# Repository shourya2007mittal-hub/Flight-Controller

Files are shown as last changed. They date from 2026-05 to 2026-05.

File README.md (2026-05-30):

# Flight Controller

I am making a STM32F405RGT6 based flight controller for my drone.and has IMU and barometer and has a USB-B Type. It is designed for 4 motor drone. It has 4 layer PCB
<br>

<br>

## Features

Microcontroller: STM32F405RGT6<br>
IMU Sensor: MPU-6050 / ICM-2098<br>
Barometer: BMP280<br>

- ## Bill of Materials (BOM)
| Serial Num | Description | Total (USD) | 
|----:|---|---|
| 1  | PCB and Assembly  |167.50 |
| 2 | Shipping - Discount JLCPCB  |14.55 |

### 💰 Cost Summary

- **Estimated Total Cost ( PCB ASSEMBLY + Shipping):** **$182.05 USD**
 ## Schematic & PCB<br>
 



<br>

# 3d Render<br>



  <br>

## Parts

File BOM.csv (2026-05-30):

Item | Price | Source
PCB and Assembly | 167.5 | JLCPCB
Shipping - Discount JLCPCB | 14.55 | JLCPCB
Total | 182.05 | JLCPCB

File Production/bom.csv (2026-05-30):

Designator | Footprint | Quantity | Value | LCSC Part #
C1, C17, C28, C29, C9 | 603 | 5 | 10u | C96446
C10, C2, C21, C22, C23, C25, C26, C27, C3, C30, C31, C4, C5, C6, C7, C8 | 402 | 16 | 100n | C1525
C11, C12 | 603 | 2 | 10p | C1634
C13, C14, C15, C16 | 603 | 4 | 2u2 | C23630
C18 | 805 | 1 | 100n | C49678
C19, C20 | 805 | 2 | 22u | C45783
C24 | 603 | 1 | 2n2 | C1604
D1, D3 | 603 | 2 | LED | C2286
D2 | D_SOD-123 | 1 | b5819w | C8598
F1 | 603 | 1 | 500 mA | C20798
FB1, FB2 | 805 | 2 | 100R | C1015
L1 | L_Sunlord_SWPA4030S | 1 | 3.9uH | C96899
Q1 | SOT-23 | 1 | AO3401A | C15127
R1 | 603 | 1 | 10k | C25804
R2, R3, R5, R6 | 603 | 4 | 2k2 | C4190
R4, R7 | 603 | 2 | 1k | C21190
S1, S2 | SW_TS-1187A-B-A-B | 2 | TS-1187A-B-A-B | C318884
U1 | LQFP-64_10x10mm_P0.5mm | 1 | STM32F405RGTx | C15742
U2 | TSOT-23-6 | 1 | AP63203WU | C780769
U3 | SOT-23-6 | 1 | USBLC6-2SC6 | C7519
U4 | InvenSense_QFN-24_4x4mm_P0.5mm | 1 | MPU-6050 | C24112
U5 | InvenSense_QFN-24_3x3mm_P0.4mm | 1 | ICM-20948 | C726001
U6 | SOT-23-5 | 1 | LD39015M18R | C361025
U7 | TSSOP-14_4.4x5mm_P0.65mm | 1 | NTS0104PW | C2802637
U8 | Bosch_LGA-8_2x2.5mm_P0.65mm_ClockwisePinNumbering | 1 | BMP280 | C83291
Y1 | Crystal_SMD_3225-4Pin_3.2x2.5mm | 1 | 16Mhz | C13738

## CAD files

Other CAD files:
CAD/Controller.f3d

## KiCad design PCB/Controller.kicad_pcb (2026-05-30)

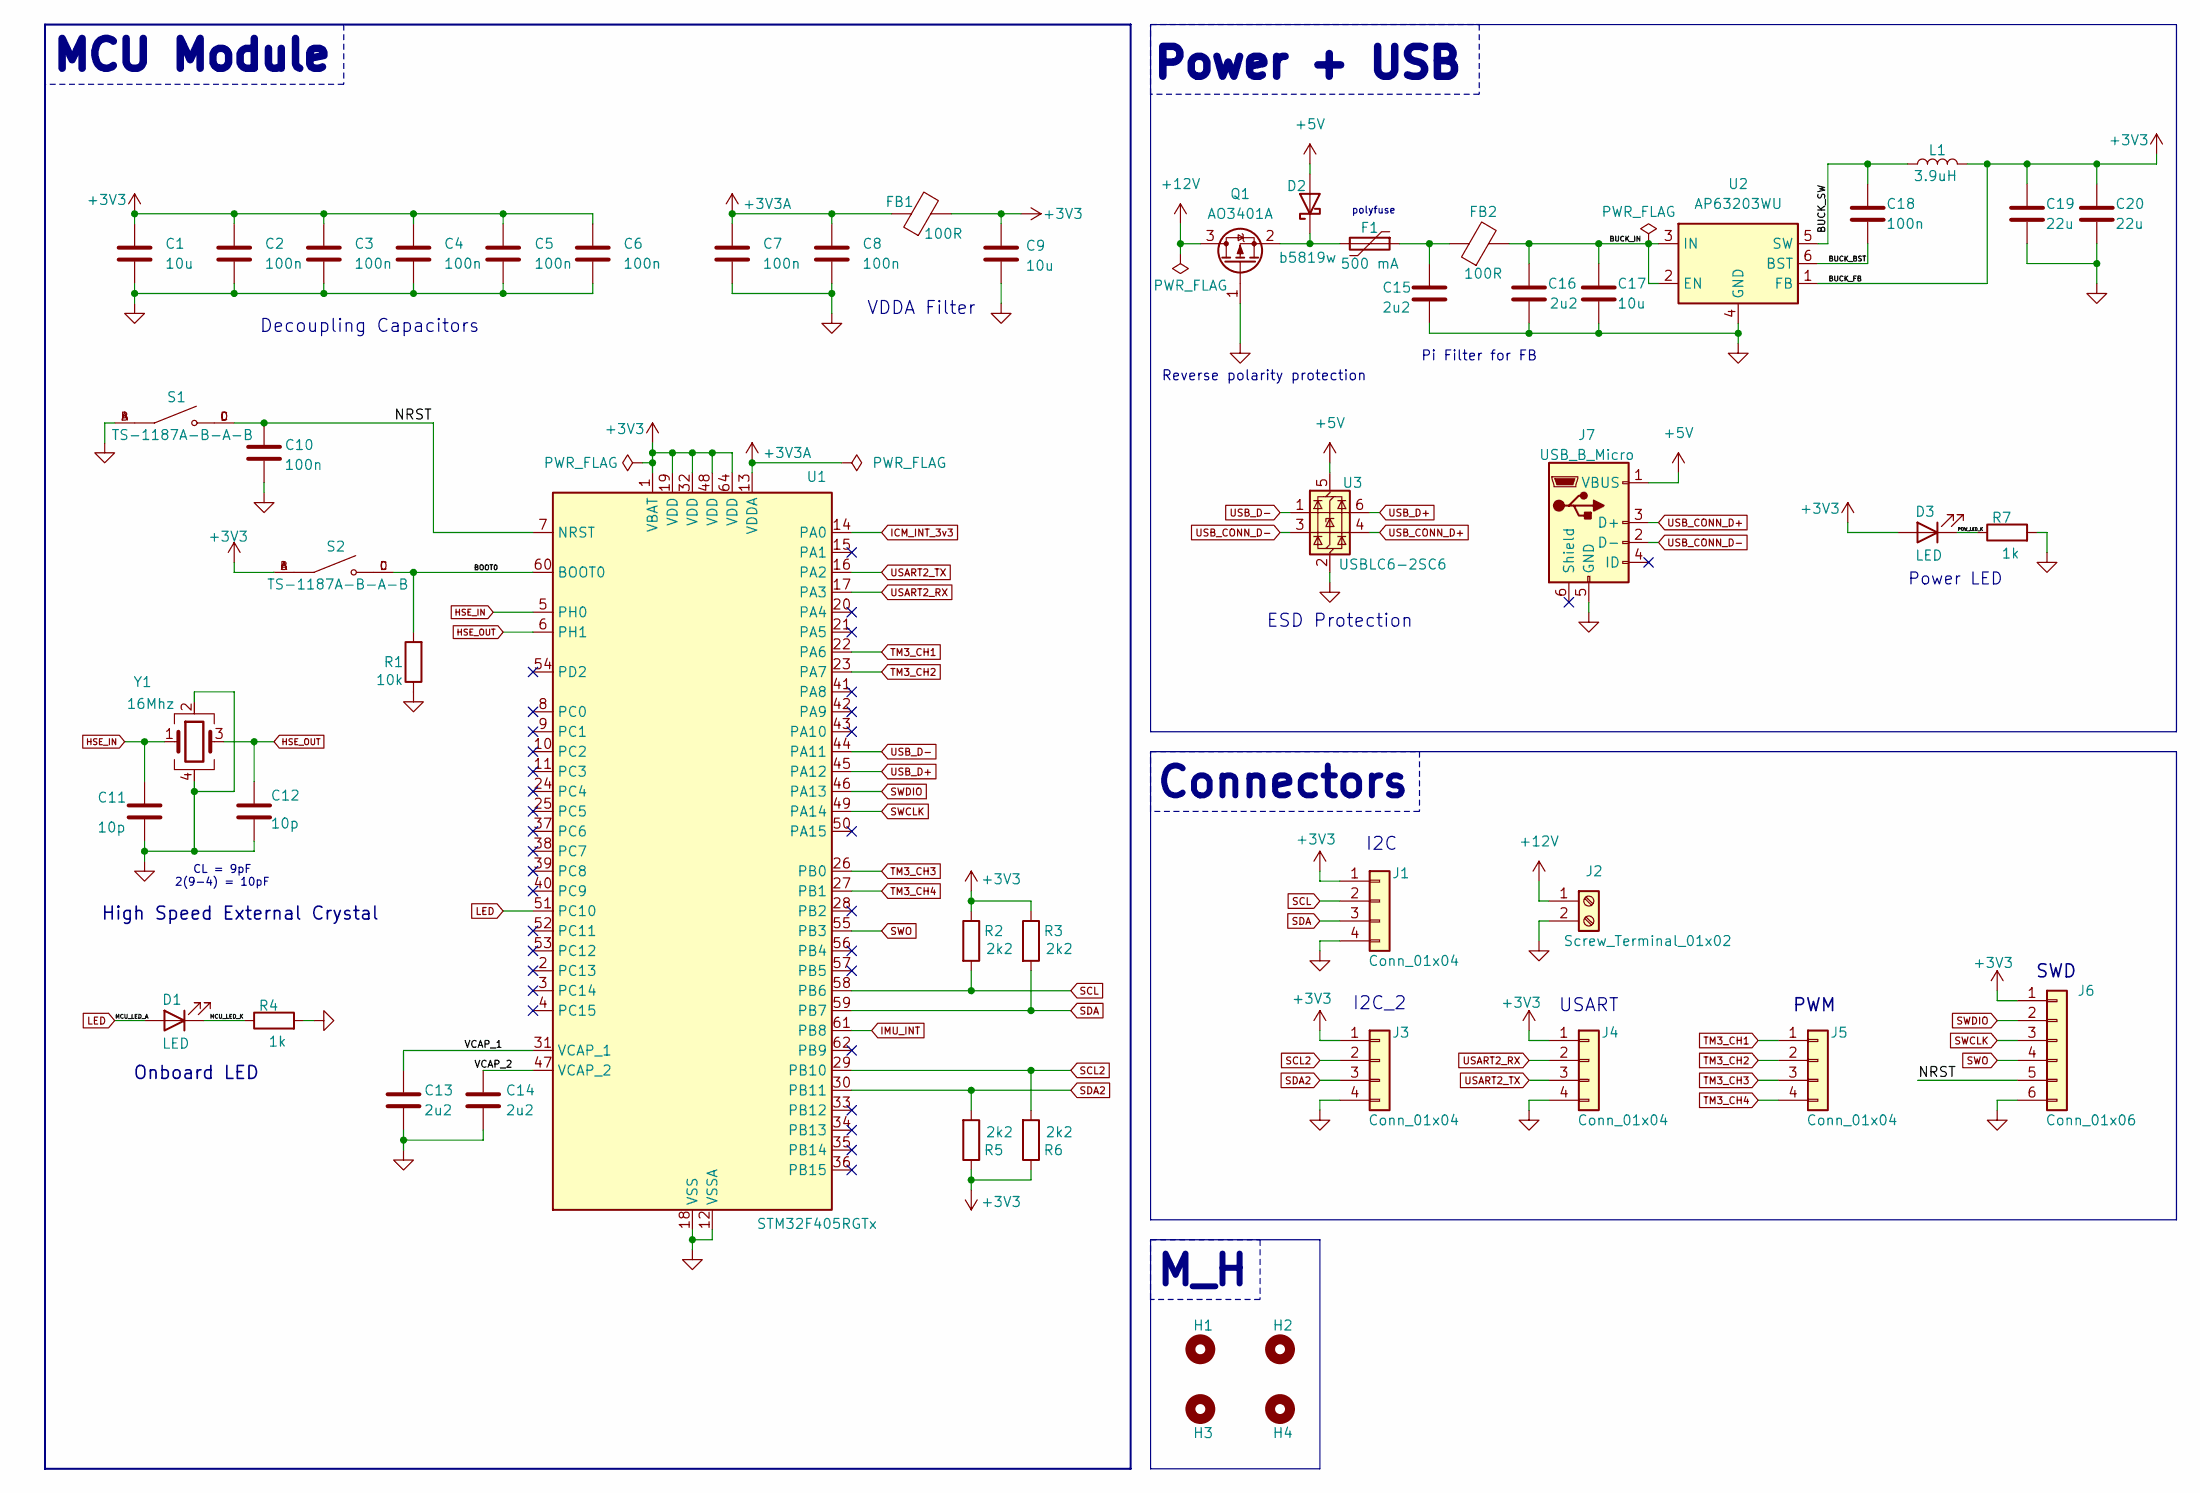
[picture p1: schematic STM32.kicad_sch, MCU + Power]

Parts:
C1, C9, C17: 10u; C_0603_1608Metric
C2, C3, C4, C5, C6, C7, C8, C10: 100n; C_0402_1005Metric
C11, C12: 10p; C_0603_1608Metric
C13, C14, C15, C16: 2u2; C_0603_1608Metric
C18: 100n; C_0805_2012Metric
C19, C20: 22u; C_0805_2012Metric
D1, D3: LED; LED_0603_1608Metric
D2: b5819w; D_SOD-123
F1: 500 mA; Fuse_0603_1608Metric
FB1, FB2: 100R; L_0805_2012Metric
H1, H2, H3, H4: MountingHole; MountingHole_4.3mm_M4_Pad_Via
J1, J3, J4, J5: Conn_01x04; PinSocket_1x04_P2.54mm_Vertical
J2: Screw_Terminal_01x02; TerminalBlock_Xinya_XY308-2.54-2P_1x02_P2.54mm_Horizontal
J6: Conn_01x06; PinSocket_1x06_P2.54mm_Vertical
J7: USB_B_Micro; USB_Micro-B_Amphenol_10118193-0001LF_Horizontal
L1: 3.9uH; L_Sunlord_SWPA4030S
Q1: AO3401A; SOT-23
R1: 10k; R_0603_1608Metric
R2, R3, R5, R6: 2k2; R_0603_1608Metric
R4, R7: 1k; R_0603_1608Metric
S1, S2: TS-1187A-B-A-B; SW_TS-1187A-B-A-B; PARTREV A0
U1: STM32F405RGTx; LQFP-64_10x10mm_P0.5mm
U2: AP63203WU; TSOT-23-6
U3: USBLC6-2SC6; SOT-23-6
Y1: 16Mhz; Crystal_SMD_3225-4Pin_3.2x2.5mm

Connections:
+3V3: C1.1, C2.1, C3.1, C4.1, C5.1, C6.1, C9.1, C19.1, C20.1, D3.2 (A), FB1.2, J1.1, J3.1, J4.1, J6.1, L1.2, R2.1, R3.1, R5.1, R6.1, S2.A, S2.B, U1.1 (VBAT), U1.19 (VDD), U1.32 (VDD), U1.48 (VDD), U1.64 (VDD), U2.1 (FB); also elsewhere on the board
+3V3A: C7.1, C8.1, FB1.1, U1.13 (VDDA)
+5V: D2.2 (A), J7.1 (VBUS), U3.5 (VBUS)
+12V: J2.1, Q1.3 (D)
/STM32/BOOT0: R1.2, S2.C, S2.D, U1.60 (BOOT0)
/STM32/BUCK_BST: C18.2, U2.6 (BST)
/STM32/BUCK_IN: C16.1, C17.1, FB2.2, U2.2 (EN), U2.3 (IN)
/STM32/BUCK_SW: C18.1, L1.1, U2.5 (SW)
/STM32/MCU_LED_K: D1.1 (K), R4.1
/STM32/NRST: C10.1, J6.5, S1.C, S1.D, U1.7 (NRST)
/STM32/POW_LED_K: D3.1 (K), R7.1
/STM32/VCAP_1: C13.1, U1.31 (VCAP_1)
/STM32/VCAP_2: C14.1, U1.47 (VCAP_2)
GND: C1.2, C2.2, C3.2, C4.2, C5.2, C6.2, C7.2, C8.2, C9.2, C10.2, C11.2, C12.2, C13.2, C14.2, C15.2, C16.2, C17.2, C19.2, C20.2, H1.1, H2.1, H3.1, H4.1, J1.4, J2.2, J3.4, J4.4, J6.6, J7.5 (GND), Q1.1 (G), R1.1, R4.2, R7.2, S1.A, S1.B, U1.12 (VSSA), U1.18 (VSS), U1.63 (VSS), U2.4 (GND), U3.2 (GND), Y1.2, Y1.4; also elsewhere on the board
HSE_IN: C11.1, U1.5 (PH0), Y1.1
HSE_OUT: C12.1, U1.6 (PH1), Y1.3
ICM_INT_3v3: U1.14 (PA0); also elsewhere on the board
IMU_INT: U1.61 (PB8); also elsewhere on the board
LED: D1.2 (A), U1.51 (PC10)
unnamed: C15.1, F1.1, FB2.1
unnamed: D2.1 (K), F1.2, Q1.2 (S)
SCL: J1.2, R2.2, U1.58 (PB6); also elsewhere on the board
SCL2: J3.2, R6.2, U1.29 (PB10); also elsewhere on the board
SDA: J1.3, R3.2, U1.59 (PB7); also elsewhere on the board
SDA2: J3.3, R5.2, U1.30 (PB11); also elsewhere on the board
SWCLK: J6.3, U1.49 (PA14)
SWDIO: J6.2, U1.46 (PA13)
SWO: J6.4, U1.55 (PB3)
TM3_CH1: J5.1, U1.22 (PA6)
TM3_CH2: J5.2, U1.23 (PA7)
TM3_CH3: J5.3, U1.26 (PB0)
TM3_CH4: J5.4, U1.27 (PB1)
USART2_RX: J4.2, U1.17 (PA3)
USART2_TX: J4.3, U1.16 (PA2)
USB_CONN_D+: J7.3 (D+), U3.4 (I/O2)
USB_CONN_D-: J7.2 (D-), U3.3 (I/O2)
USB_D+: U1.45 (PA12), U3.6 (I/O1)
USB_D-: U1.44 (PA11), U3.1 (I/O1)

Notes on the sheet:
polyfuse
ESD Protection
Decoupling Capacitors
CL = 9pF 2(9-4) = 10pF
VDDA Filter
Onboard LED
USART
M_H
Pi Filter for FB
I2C
SWD
High Speed External Crystal
Power LED
PWM
Reverse polarity protection
MCU Module
Connectors
Power + USB
I2C_2

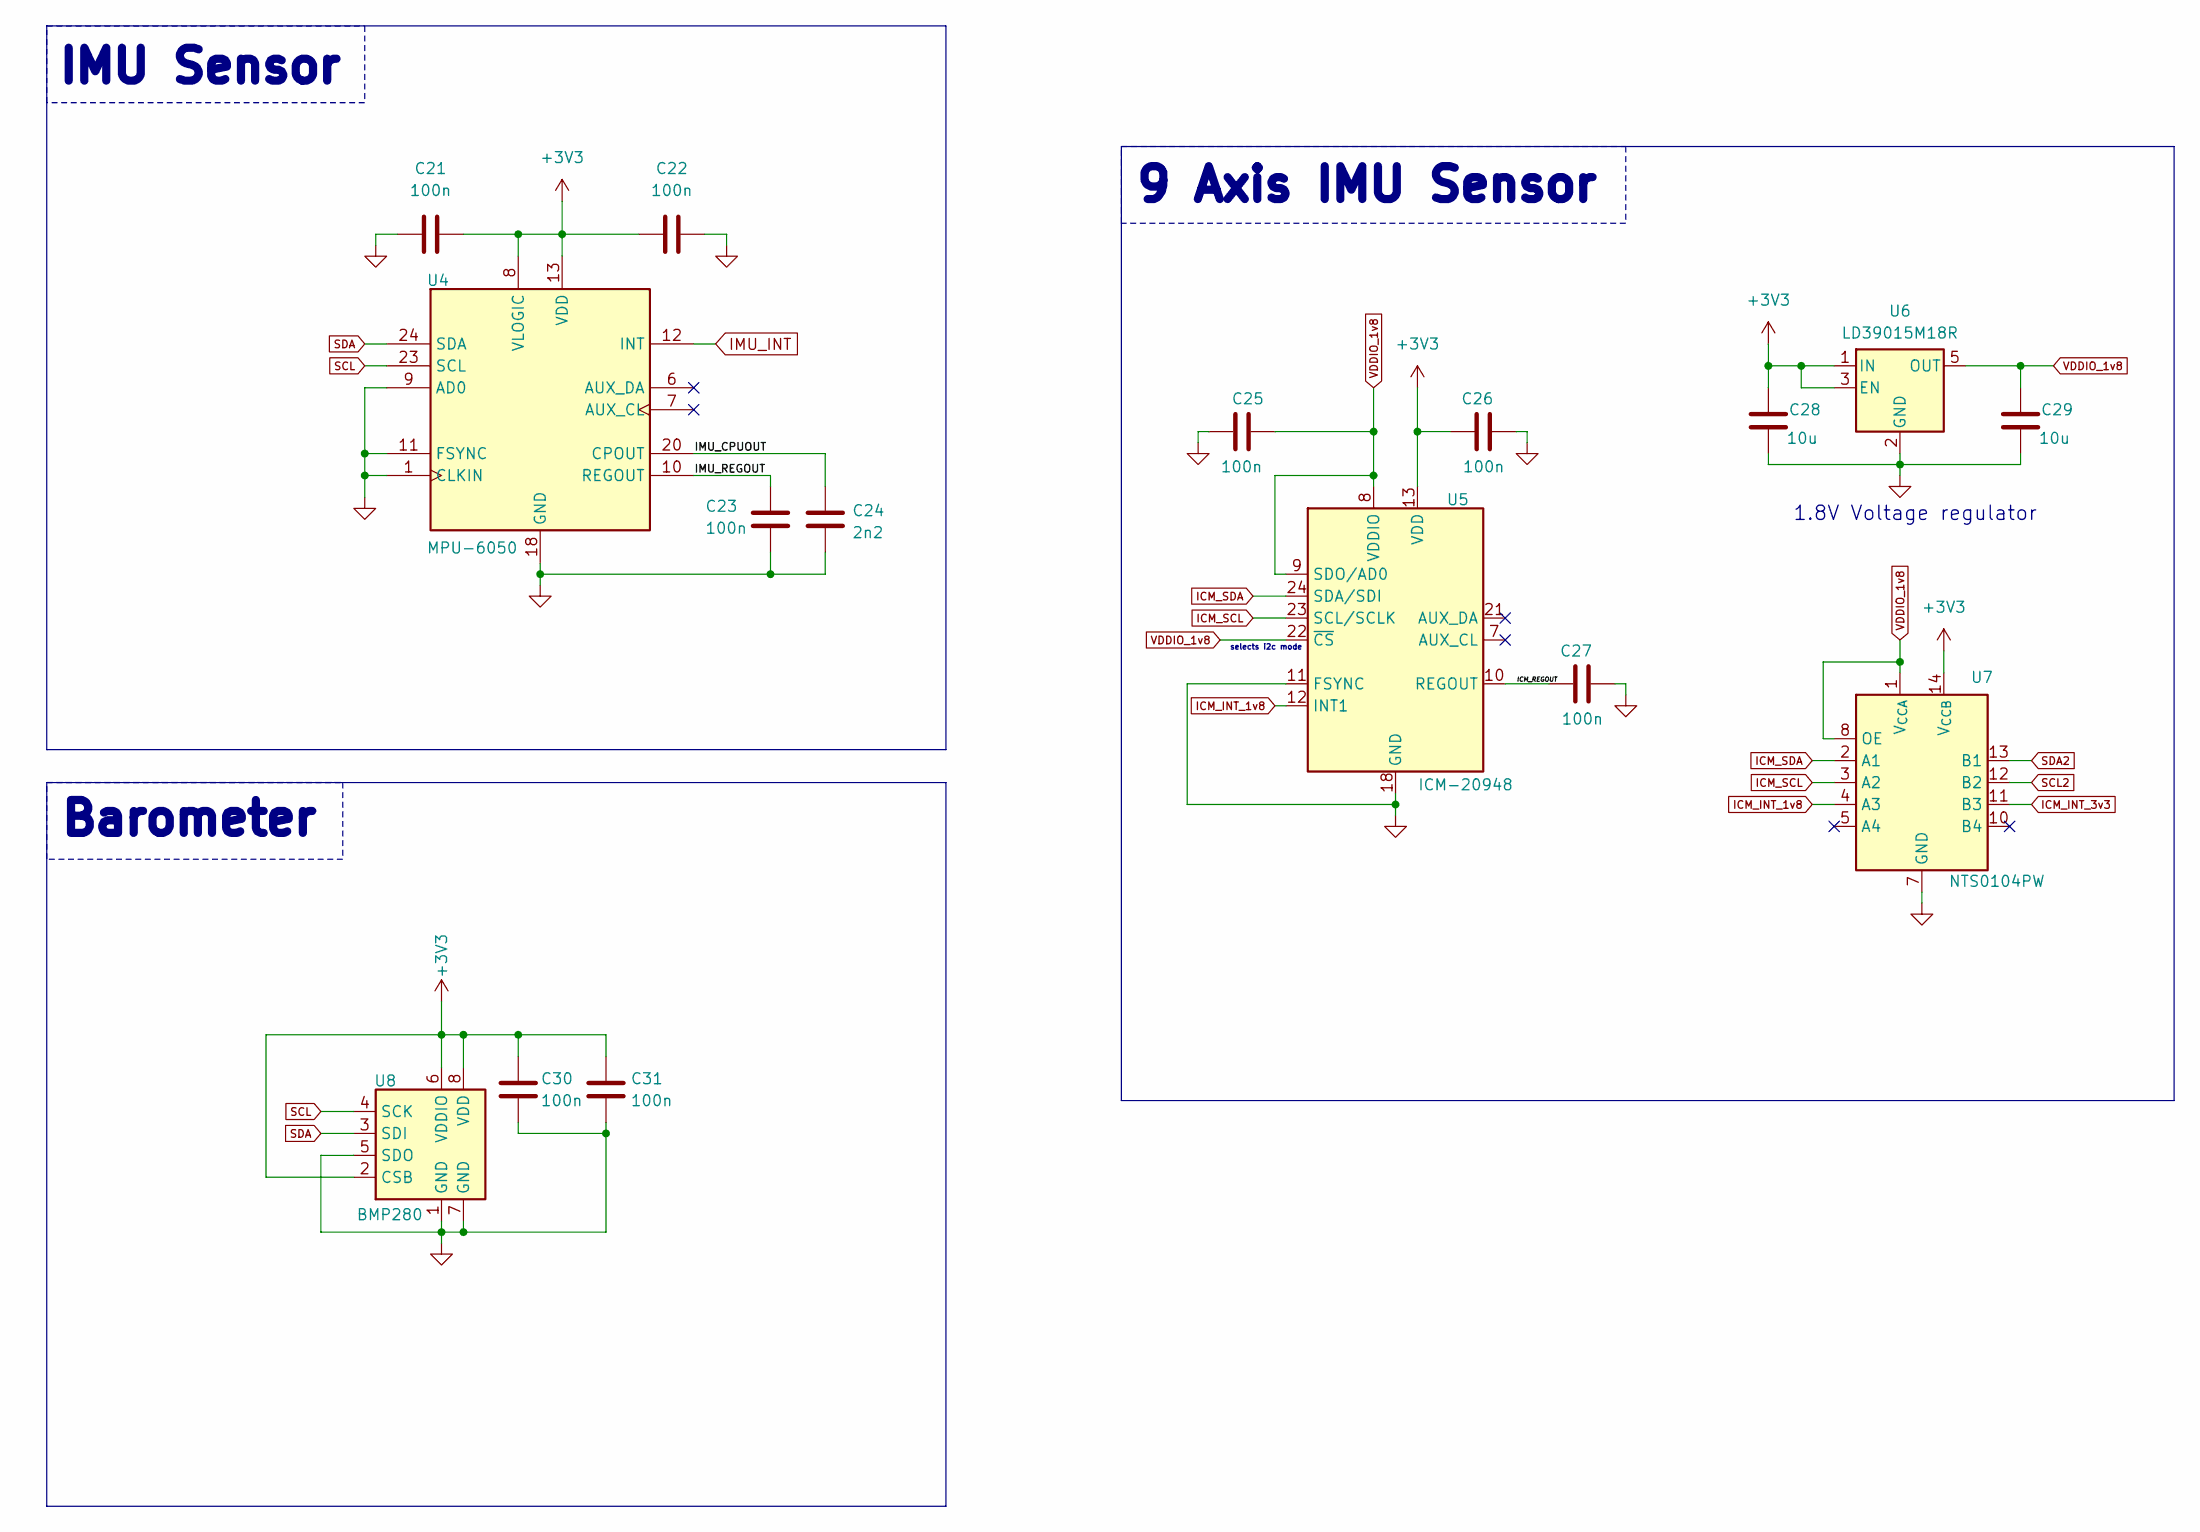
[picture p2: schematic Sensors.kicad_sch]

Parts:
C21, C22, C23, C25, C26, C27, C30, C31: 100n; C_0402_1005Metric
C24: 2n2; C_0603_1608Metric
C28, C29: 10u; C_0603_1608Metric
U4: MPU-6050; InvenSense_QFN-24_4x4mm_P0.5mm
U5: ICM-20948; InvenSense_QFN-24_3x3mm_P0.4mm
U6: LD39015M18R; SOT-23-5
U7: NTS0104PW; TSSOP-14_4.4x5mm_P0.65mm
U8: BMP280; Bosch_LGA-8_2x2.5mm_P0.65mm_ClockwisePinNumbering

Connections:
+3V3: C21.2, C22.1, C26.1, C28.1, C30.1, C31.2, U4.8 (VLOGIC), U4.13 (VDD), U5.13 (VDD), U6.1 (IN), U6.3 (EN), U7.14 (V_{CCB}), U8.2 (CSB), U8.6 (VDDIO), U8.8 (VDD); also elsewhere on the board
/Sensors/ICM_REGOUT: C27.1, U5.10 (REGOUT)
/Sensors/IMU_CPUOUT: C24.1, U4.20 (CPOUT)
/Sensors/IMU_REGOUT: C23.1, U4.10 (REGOUT)
GND: C21.1, C22.2, C23.2, C24.2, C25.2, C26.2, C27.2, C28.2, C29.2, C30.2, C31.1, U4.1 (CLKIN), U4.9 (AD0), U4.11 (FSYNC), U4.18 (GND), U5.11 (FSYNC), U5.18 (GND), U5.20 (GND), U6.2 (GND), U7.7 (GND), U8.1 (GND), U8.5 (SDO), U8.7 (GND); also elsewhere on the board
ICM_INT_1v8: U5.12 (INT1), U7.4 (A3)
ICM_INT_3v3: U7.11 (B3); also elsewhere on the board
ICM_SCL: U5.23 (SCL/SCLK), U7.3 (A2)
ICM_SDA: U5.24 (SDA/SDI), U7.2 (A1)
IMU_INT: U4.12 (INT); also elsewhere on the board
SCL: U4.23 (SCL), U8.4 (SCK); also elsewhere on the board
SCL2: U7.12 (B2); also elsewhere on the board
SDA: U4.24 (SDA), U8.3 (SDI); also elsewhere on the board
SDA2: U7.13 (B1); also elsewhere on the board
VDDIO_1v8: C25.1, C29.1, U5.8 (VDDIO), U5.9 (SDO/AD0), U5.22 (~CS), U6.5 (OUT), U7.1 (V_{CCA}), U7.8 (OE)

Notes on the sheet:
9 Axis IMU Sensor
1.8V Voltage regulator
IMU Sensor
Barometer
selects i2c mode

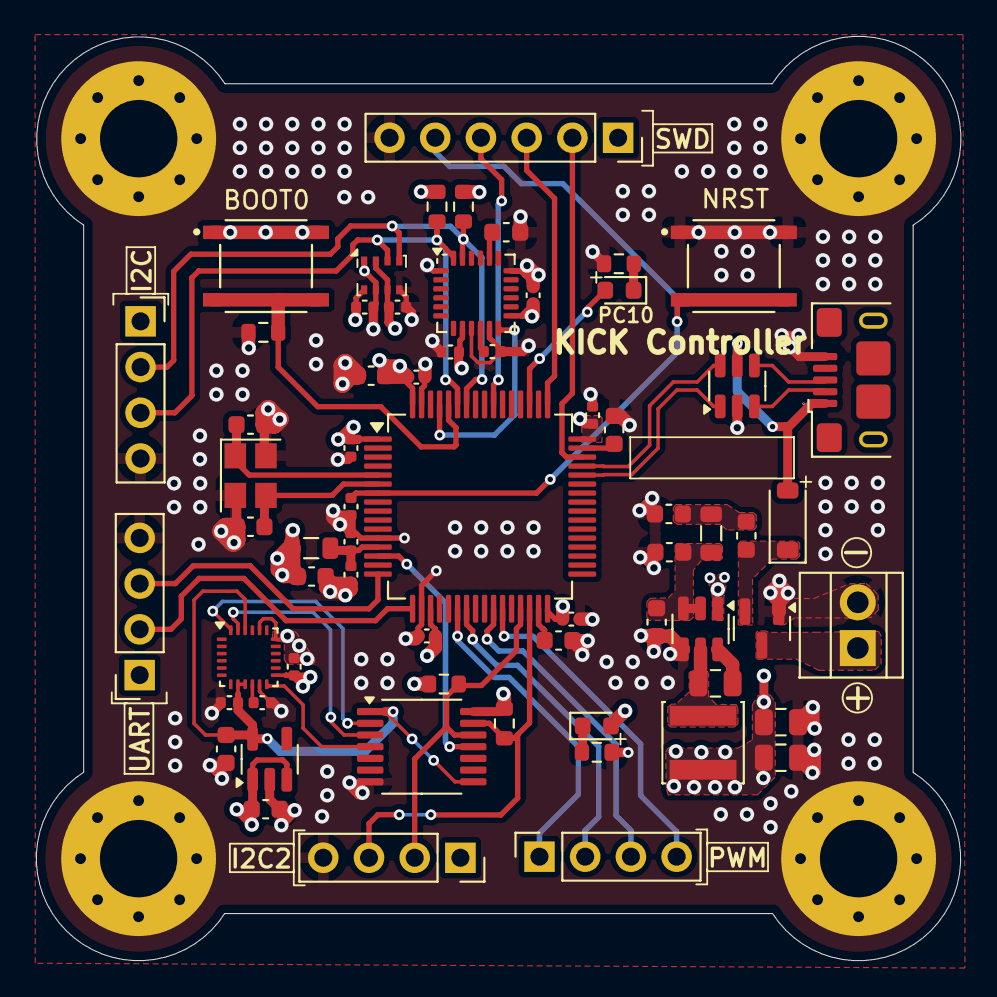
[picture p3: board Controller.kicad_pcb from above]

Board: 4 copper layers, 51.4 x 51.3 mm, 68 parts (0 on the bottom side), 45 nets.

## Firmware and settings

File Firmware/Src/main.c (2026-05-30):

#include "main.h"
#include "imu.h"
#include "pid.h"
#include "motors.h"
#include "receiver.h"

float roll;
float pitch;
float yaw;

float accelX;
float accelY;
float accelZ;

float gyroX;
float gyroY;
float gyroZ;

PID_t pidRoll;
PID_t pidPitch;
PID_t pidYaw;

float throttle;

uint32_t previousTime;
float dt;

int main(void)
{
    HAL_Init();

    Motors_Init();

    MPU6050_Init();

    PID_Init(&pidRoll, 1.4f, 0.02f, 0.04f);
    PID_Init(&pidPitch, 1.4f, 0.02f, 0.04f);
    PID_Init(&pidYaw, 2.0f, 0.00f, 0.00f);

    previousTime = HAL_GetTick();

    while(1)
    {
        uint32_t currentTime = HAL_GetTick();

        dt = (currentTime - previousTime) / 1000.0f;

        previousTime = currentTime;

        Receiver_Read();

        throttle = rxThrottle;

        MPU6050_Read_All(&accelX,
                         &accelY,
                         &accelZ,
                         &gyroX,
                         &gyroY,
                         &gyroZ);

        IMU_ComputeAngles(accelX,
                          accelY,
                          accelZ,
                          gyroX,
                          gyroY,
                          gyroZ,
                          dt,
                          &roll,
                          &pitch,
                          &yaw);

        float rollError = rxRoll - roll;
        float pitchError = rxPitch - pitch;
        float yawError = rxYaw - gyroZ;

        float rollPID = PID_Compute(&pidRoll,
                                    rollError,
                                    dt);

        float pitchPID = PID_Compute(&pidPitch,
                                     pitchError,
                                     dt);

        float yawPID = PID_Compute(&pidYaw,
                                   yawError,
                                   dt);

        float motor1 = throttle + pitchPID + rollPID - yawPID;
        float motor2 = throttle + pitchPID - rollPID + yawPID;
        float motor3 = throttle - pitchPID + rollPID + yawPID;
        float motor4 = throttle - pitchPID - rollPID - yawPID;

        Motors_Write(0, motor1);
        Motors_Write(1, motor2);
        Motors_Write(2, motor3);
        Motors_Write(3, motor4);

        HAL_Delay(1);
    }
}

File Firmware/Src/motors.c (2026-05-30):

#include "motors.h"

extern TIM_HandleTypeDef htim1;

void Motors_Init(void)
{
    HAL_TIM_PWM_Start(&htim1, TIM_CHANNEL_1);
    HAL_TIM_PWM_Start(&htim1, TIM_CHANNEL_2);
    HAL_TIM_PWM_Start(&htim1, TIM_CHANNEL_3);
    HAL_TIM_PWM_Start(&htim1, TIM_CHANNEL_4);
}

void Motors_Write(uint8_t motor, float value)
{
    if(value < 1000)
        value = 1000;

    if(value > 2000)
        value = 2000;

    switch(motor)
    {
        case 0:
            __HAL_TIM_SET_COMPARE(&htim1,
                                  TIM_CHANNEL_1,
                                  value);
            break;

        case 1:
            __HAL_TIM_SET_COMPARE(&htim1,
                                  TIM_CHANNEL_2,
                                  value);
            break;

        case 2:
            __HAL_TIM_SET_COMPARE(&htim1,
                                  TIM_CHANNEL_3,
                                  value);
            break;

        case 3:
            __HAL_TIM_SET_COMPARE(&htim1,
                                  TIM_CHANNEL_4,
                                  value);
            break;
    }
}
